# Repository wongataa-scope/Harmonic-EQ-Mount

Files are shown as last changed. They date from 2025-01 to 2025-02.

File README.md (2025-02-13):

This is my design for a GoTo telescope mount using strainwave gears (harmonic drives).  As strainwave gear telescope mounts, such as the ZWO AM5, started to become more available I thought why not make my own.

My mount is made from CNC machined aluminium, 3D printed aluminium, and 3D printed plastic.

The RA and DEC axes have a reduction ration of 450:1. The strainwave gears are 100:1 and there is 4:1 belt drive between the stepper motors and the strainwave gears.  The stepper motors are NEMA 17 size.

The strainwave gears are hollow so cables can pass through them.  This means there are no wires dangling off the telescope and mount.

The RA and DEC axes have hall sensors for automatic homing.

This mount has motorised altitude and azimuth axes so the mount does not have to be touched when polar aligning.  Everything is controlled by the computer controlling the mount.  The M4 ends of the azimuth and altitude leadscrews need to have thread locker applied before screwing into the parts they fit in to.  I use Loctite 243.

I have my mount connected to a EQ5 tripod.  The tripod interface will need to be modified if you wish to use a different tripod.  The 4040 aluminium extrusions do not have to be the length they are in the CAD files.  They can be any length.

I would recommend the CNC aluminium parts are made from 6061-T6 or 6082-T6 aluminium.  These grades are readily available, easily machined, and strong.  The T6 denotes the temper level.  T6 is stronger than non-tempered aluminium.
I used PETG for the 3D printed plastic.  I used heat set thread inserts in the 3D printed plastic where screws are screwed into them.

The first sheet of the BOM is a list of every part used.  The second sheet contains the BOMs broken down for each sub assembly.

The ‘Complete_Assembly_Neutral’ folder has a STEP and Parasolid file of the entire mount.

The ‘Solidworks_Makers_Files’ folder has the source Solidworks part, assembly, and drawing files.  These files were created in the Solidworks Makers version so cannot be opened with the educational or commercial versions of Solidworks.

The ‘Part_Drawing_PDF’ folder contains every drawing in PDF format.

The ‘3D_Print_Aluminium’ folder contains the files sent for aluminium 3D printing for the parts that underwent machining after printing.  These parts were machined on a lathe to fit bearings.

This is very much a version 1 design.  I’m sure there are ways it could be improved.  It hasn’t had much testing yet, but it does work.  I use the OpenAstroTech control system but it could also be made to work with OnStep.

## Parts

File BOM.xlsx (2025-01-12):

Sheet: Single BOM
1 | 2020 | 2020 ALUMINIUM EXTRUSION - 200 | 2 | https://ooznest.co.uk/product/20x20mm-t-v-slot-aluminium-extrusion-profile-silver-cut-to-size/
2 | 2040 | 2040 ALUMINIUM EXTRUSION - 150 | 2 | https://ooznest.co.uk/product/20x40mm-t-v-slot-aluminium-extrusion-profile-silver-cut-to-size/
3 | 4040 | 4040 ALUMINIUM EXTRUSION - 450 | 4 | https://ooznest.co.uk/product/40x40mm-t-v-slot-aluminium-extrusion-profile-silver-cut-to-size/
4 | 16 Pulley | PULLEY, GT2, 16 TOOTH | 2 | 16 Teeth, 5mm shaft, for 10mm belt |  |  | https://www.aliexpress.com/item/32995138803.html (https://www.igus.co.uk/iglidur-ibh/flanged-bearings/product-details/iglidur-g-m?artnr=GFM-0810-11)
5 | 17N13S1504FF5-200RS | AZ MOTOR | 2 | https://www.omc-stepperonline.com/nema-17-non-captive-acme-linear-stepper-motor-1-5a-34mm-stack-screw-lead-1-27mm-0-05-lead-length-200mm-17n13s1504ff5-200rs (https://www.igus.co.uk/iglidur-ibh/flanged-bearings/product-details/iglidur-g-m?artnr=GFM-0810-11)
6 | 30mm Shaft Support Seat | SUPPORT, SHAFT, 30MM | 1 | LFH 30 | https://www.aliexpress.com/item/4000088608614.html (https://www.igus.co.uk/iglidur-ibh/flanged-bearings/product-details/iglidur-g-m?artnr=GFM-0810-11)
7 | 5-M4-8 Shoulder screw |  | 1 | Berger Tools ISO7379-5-M4-8-NI |  |  | https://www.berger-tools.co.uk/Iso7379_Hexagon_Socket_Head_Shoulder_Screw_Ssb_Stainless/
8 | 72 Pulley Custom 3D Print | 72 PULLEY 3D PRINT | 2 | 3D Printed Plastic
9 | 72 Pulley Custom 3D Print Flange | 72 PULLEY FLANGE | 2 | 3D Printed Plastic
10 | Bearing Cover | BEARING COVER | 2 | 3D Printed Plastic
11 | Belt | BELT, GT2, 170 | 2 | 170 teeth 9mm wide |  | https://www.aliexpress.com/item/4000034021834.html
12 | Box Cable Guide 2 | BOX CABLE GUIDE | 1 | 3D Printed Plastic
13 | BUTTON HEAD M4x10 | SOCKET BUTTON HEAD, M4x10 | 32
14 | BUTTON HEAD M4x16 | SOCKET BUTTON HEAD M4x16 | 8
15 | BUTTON HEAD M4x20 | SOCKET BUTTON HEAD M4x20 | 2
16 | Cable Wedge | CABLE WEDGE | 1 | 3D Printed Plastic
17 | EQ5 Tripod Head | EQ5 TRIPOD HEAD | 1 | Part of tripod for reference
18 | Hall Effect Sensor | HALL EFFECT SENSOR | 2 | https://www.amazon.co.uk/WINGONEER-Effect-KY-003-Magnetic-Arduino/dp/B06XHG9CYN (https://www.igus.co.uk/iglidur-ibh/flanged-bearings/product-details/iglidur-g-m?artnr=GFM-0810-11)
19 | IGUS GFM-0810-11 | IGUS GFM-0810-11 | 4 | https://www.igus.co.uk/iglidur-ibh/flanged-bearings/product-details/iglidur-g-m?artnr=GFM-0810-11
20 | IGUS GFM-2023-11 | IGUS GFM-2023-11 | 2 | https://www.igus.co.uk/iglidur-ibh/flanged-bearings/product-details/iglidur-g-m?artnr=GFM-2023-11
21 | KFL08 | KFL08 BEARING | 2
22 | M10x55 | BOLT, HEX HD M10x55 | 1
23 | M3x10 | SCREW, SS SKT HD CAP M3x10 | 4
24 | M3x12 | SCREW, SS SKT HD CAP M3x12 | 4
25 | M3x20 | SCREW, SS SKT HD CAP M3x20 | 2
26 | M3x25 | SCREW, SS SKT HD CAP M3x25 | 34
27 | M3x30 | SCREW, SS SKT HD CAP M3x30 | 24
28 | M3x8 | SCREW, SS SKT HD CAP M3x8 | 12
29 | M4 Female Rod End Dia 5 Hole |  | 1 | Berger Tools GN648.1-5-M4-W |  |  | https://www.berger-tools.co.uk/Gn6481_Ball_Joint_Head_Female_Thread_Steel_Or_Steel_And_Brass/
30 | M4 WASHER | WASHER, SS STD HVY M4 | 4
31 | M4x10 | SCREW, SS SKT HD CAP M4x10 | 8
32 | M4x12 | SCREW, SS SKT HD CAP M4x12 | 20
33 | M5x10 | SCREW, SS SKT HD CAP M5x10 | 8
34 | M5x16 | M5x16 SS BUTTON HEAD | 36
35 | M5x25 | SCREW, SS SKT HD CAP M5x25 | 16
36 | M6x10 | SCREW, SS SKT HD CAP M6x10 | 8
37 | M6x20 | SCREW, SS SKT HD CAP M6x20 | 4
38 | M8 WASHER | WASHER, SS STD HVY M8 | 2
39 | M8x20 | SCREW, SS SKT HD CAP M8x20 | 2
40 | Magnet | MAGNET | 2 | https://www.amazon.co.uk/dp/B097MJLY51 (https://www.igus.co.uk/iglidur-ibh/flanged-bearings/product-details/iglidur-g-m?artnr=GFM-0810-11)
41 | Magnet Holder | MAGNET HOLDER | 2 | 3D Printed Plastic
42 | ML-EQHD-001 | DEC BEARING PLATE | 1 | 6061-T6 or 6082-T6 Aluminium
43 | ML-EQHD-002 | RA BEARING PLATE | 1 | 6061-T6 or 6082-T6 Aluminium
44 | ML-EQHD-003 | COUNTERWEIGHT PLATE | 1 | 6061-T6 or 6082-T6 Aluminium
45 | ML-EQHD-004 | TOP PLATE | 1 | 6061-T6 or 6082-T6 Aluminium
46 | ML-EQHD-005 | SIDE PLATE | 2 | 6061-T6 or 6082-T6 Aluminium
47 | ML-EQHD-006 | DEC PLATE | 1 | 6061-T6 or 6082-T6 Aluminium
48 | ML-EQHD-007 | VIXEN CLAMP PLATE | 1 | 6061-T6 or 6082-T6 Aluminium
49 | ML-EQHD-008 | RA PLATE | 1 | 6061-T6 or 6082-T6 Aluminium
50 | ML-EQHD-009 | RA SIDE PLATE | 2 | 6061-T6 or 6082-T6 Aluminium
51 | ML-EQHD-010 | ALT PIVOT UPRIGHT | 2 | 6061-T6 or 6082-T6 Aluminium
52 | ML-EQHD-011 | ALT PIVOT BASE | 1 | 6061-T6 or 6082-T6 Aluminium
53 | ML-EQHD-013 | AZ FRAME BASE | 1 | 6061-T6 or 6082-T6 Aluminium
54 | ML-EQHD-014 | UPPER TRIPOD CONNECTION PLATE | 1 | 6061-T6 or 6082-T6 Aluminium
55 | ML-EQHD-015 | LOWER TRIPOD CONNECTION PLATE | 1 | 6061-T6 or 6082-T6 Aluminium
56 | ML-EQHD-016 | UPPER AZ MOTOR MOUNT | 1 | 6061-T6 or 6082-T6 Aluminium
57 | ML-EQHD-017 | LOWER AZ MOTOR MOUNT | 1
58 | ML-EQHD-018 | ALT PIVOT SHAFT | 1 | 6061-T6 or 6082-T6 Aluminium
59 | ML-EQHD-019 | LEADSCREW END PIVOT | 1 | 3D Printed aluminium, then machined
60 | ML-EQHD-020 | AZ MOTOR MOUNT | 1 | 3D Printed aluminium, then machined
61 | ML-EQHD-021 | AZ PIN BLOCK | 1
62 | ML-EQHD-022 | AZ MOTOR MOUNT | 1 | 3D Printed aluminium, then machined
63 | Motor Bracket MC Box | MOUNT, MOTOR, NEMA 17 | 2
64 | NEMA 17 Stepper | MOTOR, STEPPER, NEMA 17 | 2
65 | SHG-17-100-2UH | GEAR, STRAINWAVE | 2 | HBK17 100:1 |  | https://www.aliexpress.com/item/1005006392747447.html (https://www.igus.co.uk/iglidur-ibh/flanged-bearings/product-details/iglidur-g-m?artnr=GFM-0810-11)
66 | SKF_51100 | 51100 THRUST BEARING | 1
67 | SKF_51115 | 51115 THRUST BEARING | 1
68 | Tee-Nut | T NUT M5 | 28
69 | Tee-Nut | T NUT M4 | 8
70 | Thrust Bearing Cover | THRUST BEARING COVER | 1 | 3D Printed Plastic
71 | Vixen Clamp | VIXEN DOVETAIL CLAMP | 2 | https://www.firstlightoptics.com/dovetails-saddles-clamps/astro-essentials-mini-vixen-style-dovetail-clamp.html (https://www.igus.co.uk/iglidur-ibh/flanged-bearings/product-details/iglidur-g-m?artnr=GFM-0810-11)

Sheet: Assembly BOMs
Mount Complete
ITEM NO. | PART NUMBER | DESCRIPTION | QTY.
1 | Axis Box MC Parts | AXIS BOX | 1 | Assembly
2 | DEC Assy | DEC ASSEMBLY | 1 | Assembly
3 | M3x25 | SCREW, SS SKT HD CAP M3x25 | 32
4 | RA Tilt Assy | RA TILT ASSEMBLY | 1 | Assembly
5 | M5x16 | M5x16 SS BUTTON HEAD | 8
6 | Tee-Nut | T NUT M5 | 12
7 | Bearing Cover | BEARING COVER | 2 | 3D Printed Plastic
8 | BUTTON HEAD M4x10 | SOCKET BUTTON HEAD, M4x10 | 8
9 | Tripod Connection | TRIPOD CONNECTION | 1 | Assembly
10 | KFL08 | KFL08 BEARING | 2
11 | SKF_51100 | 51100 THRUST BEARING | 1
12 | M10x55 | BOLT, HEX HD M10x55 | 1
13 | AZ Frame Harmonic | AZ FRAME HARMONIC | 1 | Assembly
14 | ML-EQHD-021 | AZ PIN BLOCK | 1
15 | Hall Effect Sensor | HALL EFFECT SENSOR | 2 | https://www.amazon.co.uk/WINGONEER-Effect-KY-003-Magnetic-Arduino/dp/B06XHG9CYN (https://www.igus.co.uk/iglidur-ibh/flanged-bearings/product-details/iglidur-g-m?artnr=GFM-0810-11)
16 | 17N13S1504FF5-200RS | AZ MOTOR | 1 | https://www.omc-stepperonline.com/nema-17-non-captive-acme-linear-stepper-motor-1-5a-34mm-stack-screw-lead-1-27mm-0-05-lead-length-200mm-17n13s1504ff5-200rs (https://www.igus.co.uk/iglidur-ibh/flanged-bearings/product-details/iglidur-g-m?artnr=GFM-0810-11)
17 | ML-EQHD-022 | AZ MOTOR MOUNT | 1 | 3D Printed aluminium, then machined
18 | M3x10 | SCREW, SS SKT HD CAP M3x10 | 4
19 | M4 Female Rod End Dia 5 Hole |  | 1 | Berger Tools GN648.1-5-M4-W |  |  | https://www.berger-tools.co.uk/Gn6481_Ball_Joint_Head_Female_Thread_Steel_Or_Steel_And_Brass/
20 | 5-M4-8 Shoulder screw |  | 1 | Berger Tools ISO7379-5-M4-8-NI |  |  | https://www.berger-tools.co.uk/Iso7379_Hexagon_Socket_Head_Shoulder_Screw_Ssb_Stainless/
21 | Thrust Bearing Cover | THRUST BEARING COVER | 1 | 3D Printed Plastic
22 | M4 WASHER | WASHER, SS STD HVY M4 | 4
23 | M4x12 | SCREW, SS SKT HD CAP M4x12 | 4
24 | BUTTON HEAD M4x20 | SOCKET BUTTON HEAD M4x20 | 2
25 | M5x16 | SCREW, SS SKT HD CAP M5x16 | 4
Axis Box MC Parts
ITEM NO. | Number | DESCRIPTION | QTY.
1 | ML-EQHD-001 | DEC BEARING PLATE | 1 | 6061-T6 or 6082-T6 Aluminium
2 | ML-EQHD-002 | RA BEARING PLATE | 1 | 6061-T6 or 6082-T6 Aluminium
3 | SHG-17-100-2UH | GEAR, STRAINWAVE | 2 | HBK17 100:1 |  | https://www.aliexpress.com/item/1005006392747447.html (https://www.igus.co.uk/iglidur-ibh/flanged-bearings/product-details/iglidur-g-m?artnr=GFM-0810-11)
4 | 72 Pulley Custom 3D Print | 72 PULLEY 3D PRINT | 2 | 3D Printed Plastic
5 | 72 Pulley Custom 3D Print Flange | 72 PULLEY FLANGE | 2 | 3D Printed Plastic
6 | M3x8 | SCREW, SS SKT HD CAP M3x8 | 6
7 | ML-EQHD-003 | COUNTERWEIGHT PLATE | 1 | 6061-T6 or 6082-T6 Aluminium
8 | 16 Pulley | PULLEY, GT2, 16 TOOTH | 2 | 16 Teeth, 5mm shaft, for 10mm belt |  |  | https://www.aliexpress.com/item/32995138803.html (https://www.igus.co.uk/iglidur-ibh/flanged-bearings/product-details/iglidur-g-m?artnr=GFM-0810-11)
9 | Belt | BELT, GT2, 170 | 2 | 170 teeth 9mm wide |  | https://www.aliexpress.com/item/4000034021834.html
10 | NEMA 17 Stepper | MOTOR, STEPPER, NEMA 17 | 2
11 | ML-EQHD-004 | TOP PLATE | 1 | 6061-T6 or 6082-T6 Aluminium
12 | Motor Bracket MC Box | MOUNT, MOTOR, NEMA 17 | 2
13 | ML-EQHD-005 | SIDE PLATE | 2 | 6061-T6 or 6082-T6 Aluminium
14 | 30mm Shaft Support Seat | SUPPORT, SHAFT, 30MM | 1 | LFH 30 | https://www.aliexpress.com/item/4000088608614.html (https://www.igus.co.uk/iglidur-ibh/flanged-bearings/product-details/iglidur-g-m?artnr=GFM-0810-11)
15 | M6x20 | SCREW, SS SKT HD CAP M6x20 | 4
16 | M3x30 | SCREW, SS SKT HD CAP M3x30 | 24
17 | M4x12 | SCREW, SS SKT HD CAP M4x12 | 8
18 | BUTTON HEAD M4x10 | SOCKET BUTTON HEAD, M4x10 | 24
19 | M3x25 | SCREW, SS SKT HD CAP M3x25 | 2
20 | Box Cable Guide 2 | BOX CABLE GUIDE | 1 | 3D Printed Plastic
21 | M3x20 | SCREW, SS SKT HD CAP M3x20 | 2
DEC Assy
ITEM NO. | PART NUMBER | DESCRIPTION | QTY.
1 | ML-EQHD-006 | DEC PLATE | 1 | 6061-T6 or 6082-T6 Aluminium
2 | 2020 | 2020 ALUMINIUM EXTRUSION - 200 | 2 | https://ooznest.co.uk/product/20x20mm-t-v-slot-aluminium-extrusion-profile-silver-cut-to-size/
3 | Tee-Nut | T NUT M5 | 8
4 | M5x16 | M5x16 SS BUTTON HEAD | 8
5 | ML-EQHD-007 | VIXEN CLAMP PLATE | 1 | 6061-T6 or 6082-T6 Aluminium
6 | Vixen Clamp | VIXEN DOVETAIL CLAMP | 2 | https://www.firstlightoptics.com/dovetails-saddles-clamps/astro-essentials-mini-vixen-style-dovetail-clamp.html (https://www.igus.co.uk/iglidur-ibh/flanged-bearings/product-details/iglidur-g-m?artnr=GFM-0810-11)
7 | M6x10 | SCREW, SS SKT HD CAP M6x10 | 8
8 | M4x10 | SCREW, SS SKT HD CAP M4x10 | 8
9 | Tee-Nut | T NUT M4 | 8
10 | Magnet Holder | MAGNET HOLDER | 1 | 3D Printed Plastic
11 | Magnet | MAGNET | 1 | https://www.amazon.co.uk/dp/B097MJLY51 (https://www.igus.co.uk/iglidur-ibh/flanged-bearings/product-details/iglidur-g-m?artnr=GFM-0810-11)
12 | M3x8 | SCREW, SS SKT HD CAP M3x8 | 2
RA Tilt Assy
ITEM NO. | PART NUMBER | DESCRIPTION | QTY.
1 | ML-EQHD-008 | RA PLATE | 1 | 6061-T6 or 6082-T6 Aluminium
2 | ML-EQHD-009 | RA SIDE PLATE | 2 | 6061-T6 or 6082-T6 Aluminium
3 | BUTTON HEAD M4x16 | SOCKET BUTTON HEAD M4x16 | 8
4 | IGUS GFM-2023-11 | IGUS GFM-2023-11 | 2 | https://www.igus.co.uk/iglidur-ibh/flanged-bearings/product-details/iglidur-g-m?artnr=GFM-2023-11
5 | ML-EQHD-010 | ALT PIVOT UPRIGHT | 2 | 6061-T6 or 6082-T6 Aluminium
6 | ML-EQHD-018 | ALT PIVOT SHAFT | 1 | 6061-T6 or 6082-T6 Aluminium
7 | M8 WASHER | WASHER, SS STD HVY M8 | 2
8 | M8x20 | SCREW, SS SKT HD CAP M8x20 | 2
9 | ML-EQHD-011 | ALT PIVOT BASE | 1 | 6061-T6 or 6082-T6 Aluminium
10 | M4x12 | SCREW, SS SKT HD CAP M4x12 | 8
11 | ML-EQHD-019 | LEADSCREW END PIVOT | 1 | 3D Printed aluminium, then machined
12 | 17N13S1504FF5-200RS | AZ MOTOR | 1 | https://www.omc-stepperonline.com/nema-17-non-captive-acme-linear-stepper-motor-1-5a-34mm-stack-screw-lead-1-27mm-0-05-lead-length-200mm-17n13s1504ff5-200rs (https://www.igus.co.uk/iglidur-ibh/flanged-bearings/product-details/iglidur-g-m?artnr=GFM-0810-11)
13 | ML-EQHD-020 | AZ MOTOR MOUNT | 1 | 3D Printed aluminium, then machined
14 | IGUS GFM-0810-11 | IGUS GFM-0810-11 | 4 | https://www.igus.co.uk/iglidur-ibh/flanged-bearings/product-details/iglidur-g-m?artnr=GFM-0810-11
15 | Magnet Holder | MAGNET HOLDER | 1 | 3D Printed Plastic
16 | Magnet | MAGNET | 1 | https://www.amazon.co.uk/dp/B097MJLY51 (https://www.igus.co.uk/iglidur-ibh/flanged-bearings/product-details/iglidur-g-m?artnr=GFM-0810-11)
17 | M3x8 | SCREW, SS SKT HD CAP M3x8 | 2
18 | M3x12 | SCREW, SS SKT HD CAP M3x12 | 4
Tripod Connection
ITEM NO. | PART NUMBER | DESCRIPTION | QTY.
1 | EQ5 Tripod Head | EQ5 TRIPOD HEAD | 1 | Part of tripod for reference
2 | ML-EQHD-015 | LOWER TRIPOD CONNECTION PLATE | 1 | 6061-T6 or 6082-T6 Aluminium
3 | 4040 | 4040 ALUMINIUM EXTRUSION - 450 | 4 | https://ooznest.co.uk/product/40x40mm-t-v-slot-aluminium-extrusion-profile-silver-cut-to-size/
4 | M5x16 | SCREW, SS SKT HD CAP M5x16 | 16
5 | ML-EQHD-014 | UPPER TRIPOD CONNECTION PLATE | 1 | 6061-T6 or 6082-T6 Aluminium
6 | ML-EQHD-016 | UPPER AZ MOTOR MOUNT | 1 | 6061-T6 or 6082-T6 Aluminium
7 | M5x25 | SCREW, SS SKT HD CAP M5x25 | 16
8 | SKF_51115 | 51115 THRUST BEARING | 1
9 | ML-EQHD-017 | LOWER AZ MOTOR MOUNT | 1
AZ Frame Harmonic
ITEM NO. | PART NUMBER | DESCRIPTION | QTY.
1 | ML-EQHD-013 | AZ FRAME BASE | 1 | 6061-T6 or 6082-T6 Aluminium
2 | 2040 | 2040 ALUMINIUM EXTRUSION - 150 | 2 | https://ooznest.co.uk/product/20x40mm-t-v-slot-aluminium-extrusion-profile-silver-cut-to-size/
3 | Tee-Nut | T NUT M5 | 8
4 | M5x10 | SCREW, SS SKT HD CAP M5x10 | 8
5 | Cable Wedge | CABLE WEDGE | 1 | 3D Printed Plastic
6 | M3x8 | SCREW, SS SKT HD CAP M3x8 | 2

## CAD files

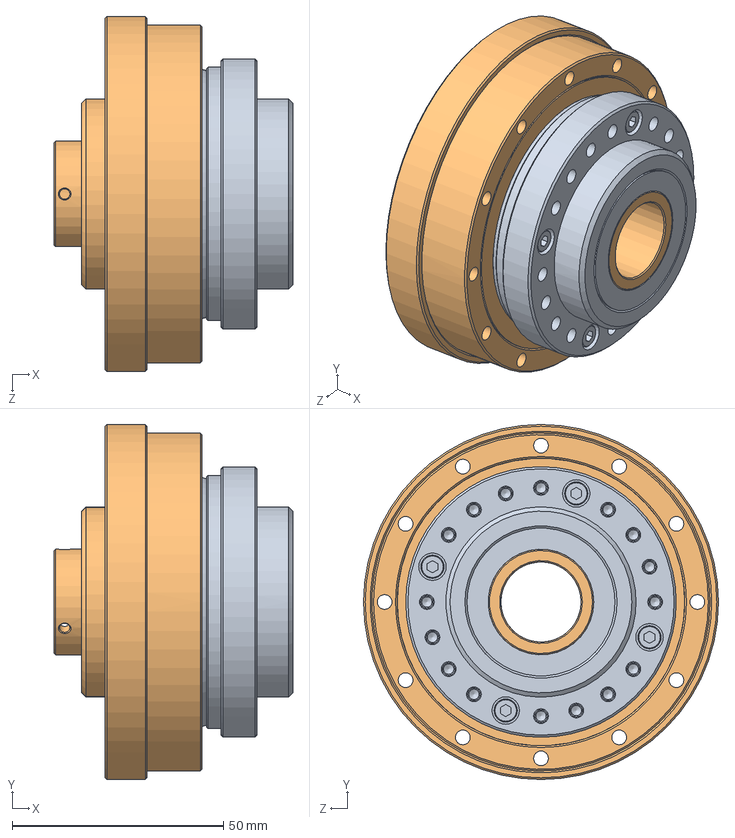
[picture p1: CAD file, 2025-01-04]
Solidworks_Makers_Files/SHG-17-100-2UH.SLDASM
56.5 x 84.0 x 84.0 mm
SHF_SHG-17-xxx-2UH-Part1
SHF_SHG-17-xxx-2UH-Part2

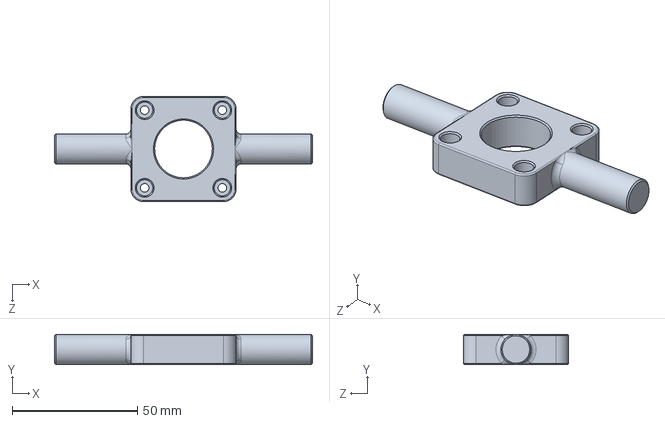
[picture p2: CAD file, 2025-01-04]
3D_Print_Aluminium/ML-EQHD-022 3D Print Al.STEP
103.0 x 12.0 x 42.0 mm

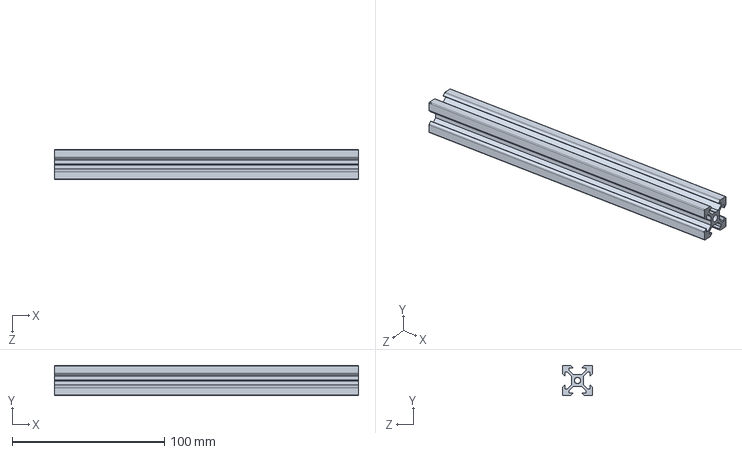
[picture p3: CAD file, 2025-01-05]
Solidworks_Makers_Files/2020.SLDPRT
200.0 x 20.0 x 20.0 mm

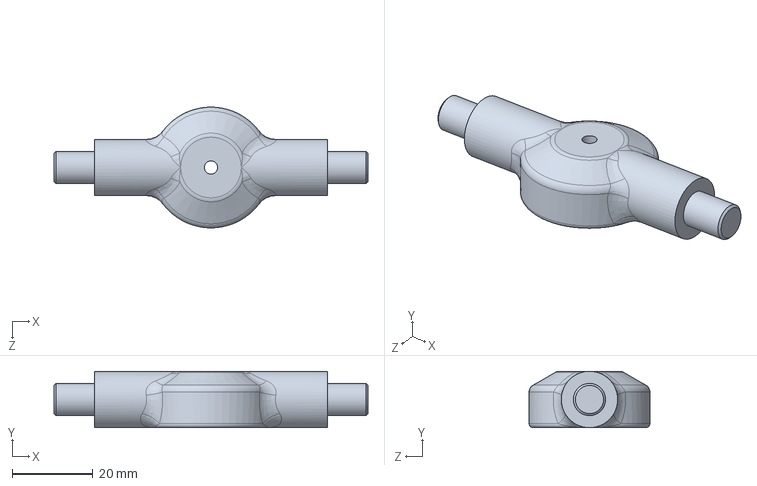
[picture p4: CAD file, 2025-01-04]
3D_Print_Aluminium/ML-EQHD-019 3D Print Al.STEP
78.0 x 14.0 x 30.0 mm

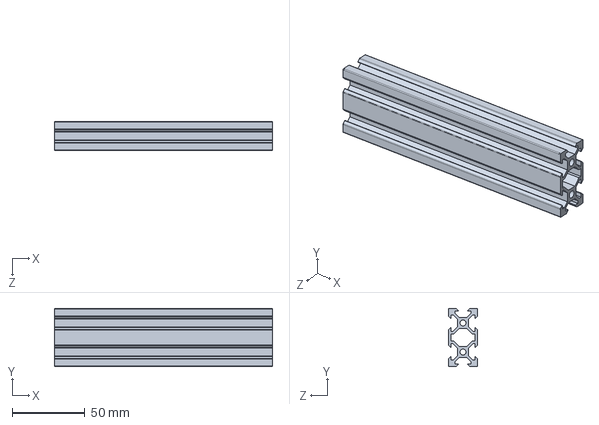
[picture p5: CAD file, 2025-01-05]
Solidworks_Makers_Files/2040.SLDPRT
150.0 x 40.0 x 20.0 mm

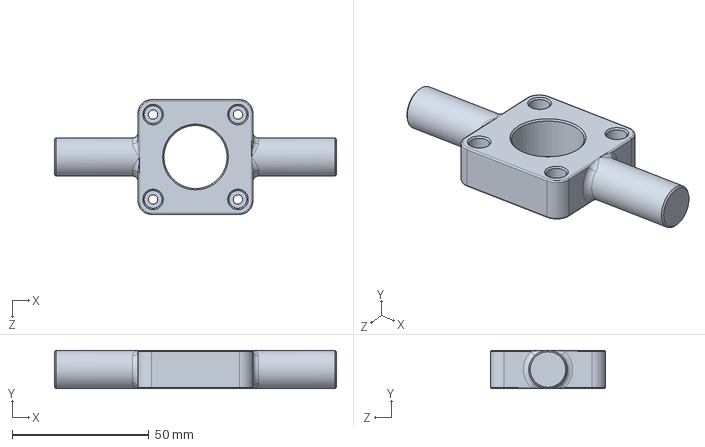
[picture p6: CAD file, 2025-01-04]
3D_Print_Aluminium/ML-EQHD-020 3D Print Al.STEP
103.0 x 14.0 x 42.0 mm

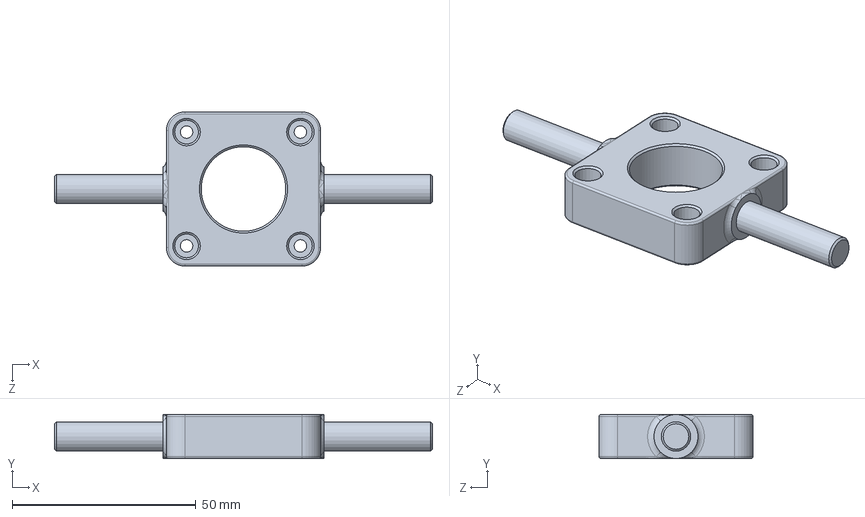
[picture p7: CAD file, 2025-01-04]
Solidworks_Makers_Files/ML-EQHD-022.SLDPRT
103.0 x 12.0 x 42.0 mm

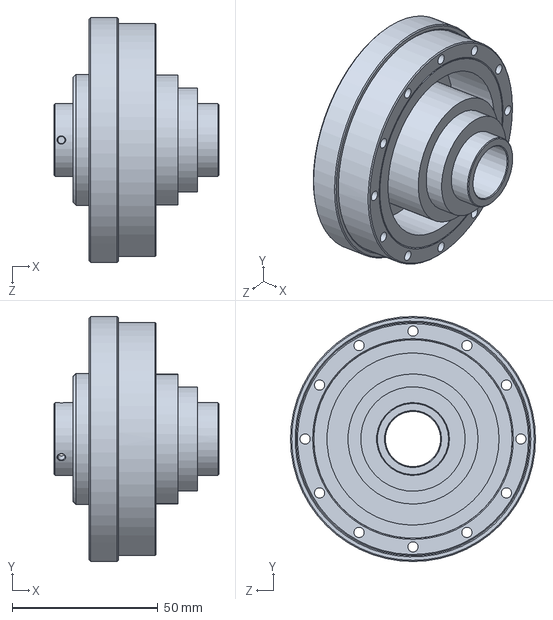
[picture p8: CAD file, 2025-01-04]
Solidworks_Makers_Files/SHF_SHG-17-xxx-2UH-Part1.SLDPRT
56.5 x 84.0 x 84.0 mm

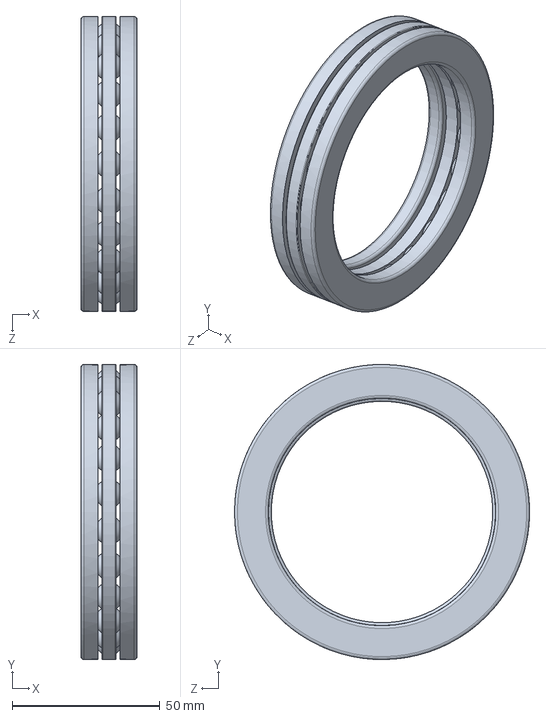
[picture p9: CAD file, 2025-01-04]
Solidworks_Makers_Files/SKF_51115.SLDPRT
19.0 x 100.0 x 100.0 mm

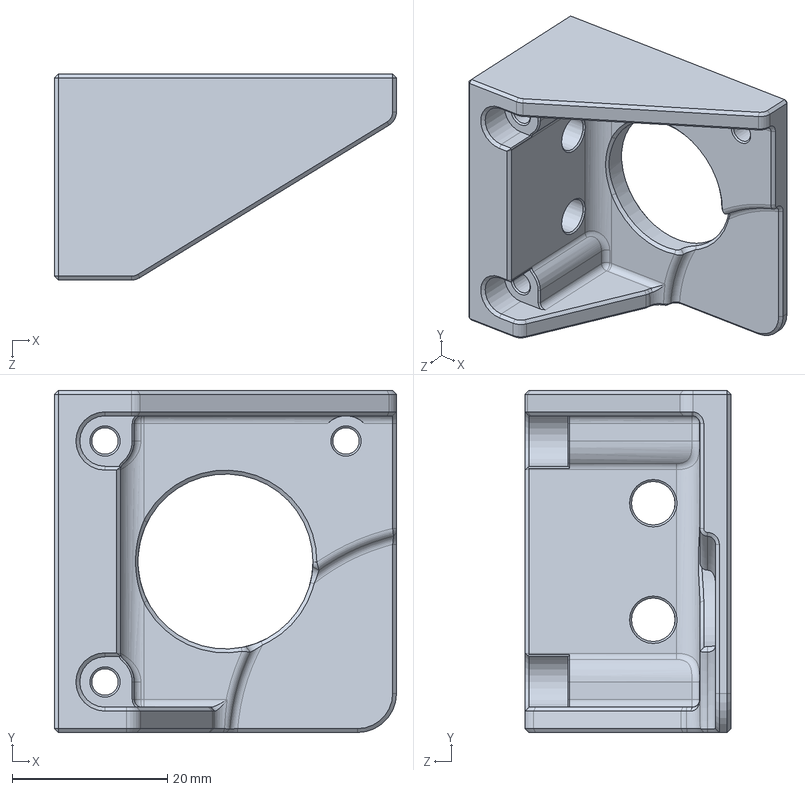
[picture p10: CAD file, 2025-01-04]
Solidworks_Makers_Files/Motor Bracket MC Box.SLDPRT
44.0 x 44.0 x 26.5 mm

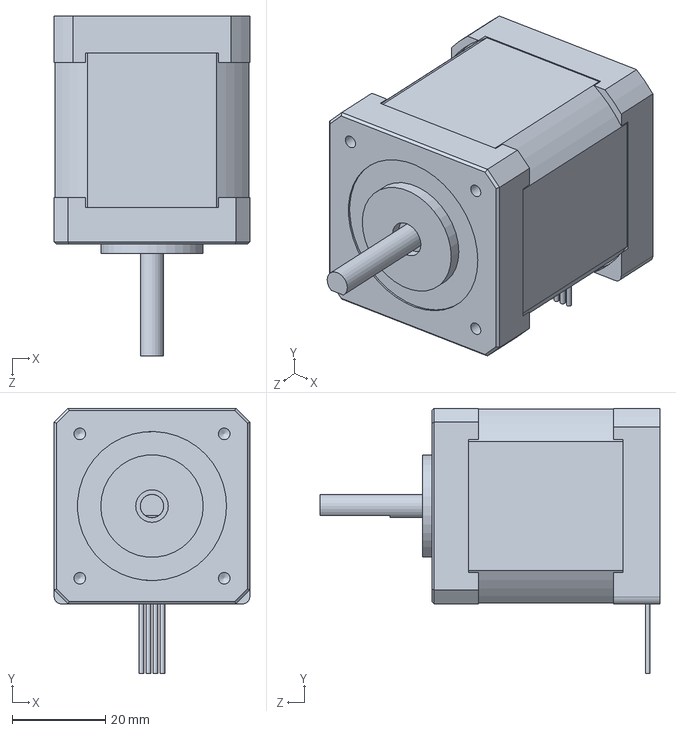
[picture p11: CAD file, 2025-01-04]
Solidworks_Makers_Files/NEMA 17 Stepper.SLDPRT
42.0 x 57.0 x 73.0 mm

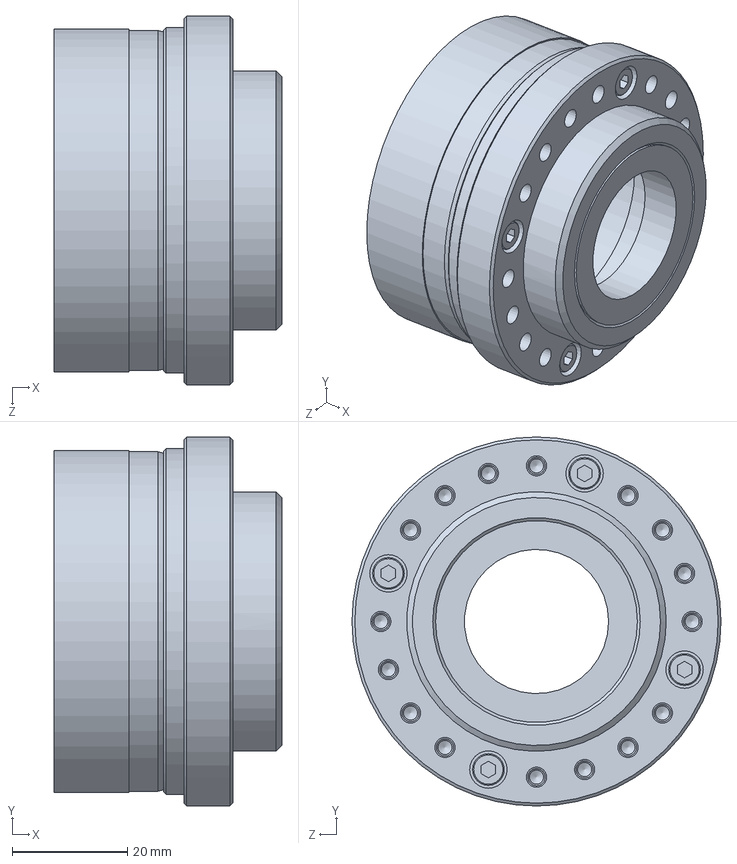
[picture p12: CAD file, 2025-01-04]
Solidworks_Makers_Files/SHF_SHG-17-xxx-2UH-Part2.SLDPRT
39.5 x 64.0 x 64.0 mm

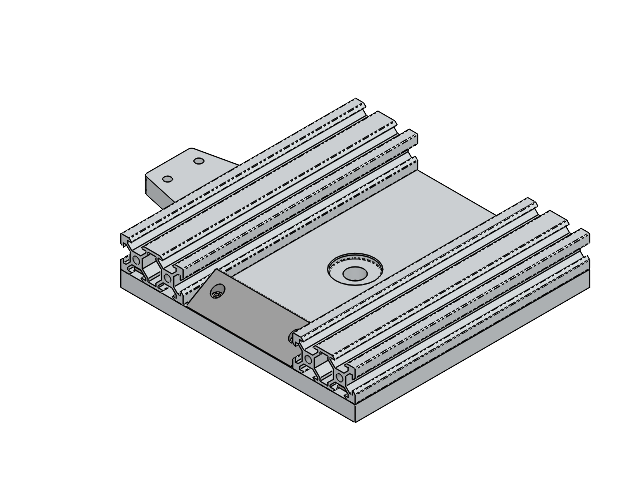
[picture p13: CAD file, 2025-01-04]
Solidworks_Makers_Files/AZ Frame Harmonic.SLDASM
ML-EQHD-013
Tee-Nut x 8
M5 SS SHCS x 8
Cable Wedge
M3 SS SHCS x 2

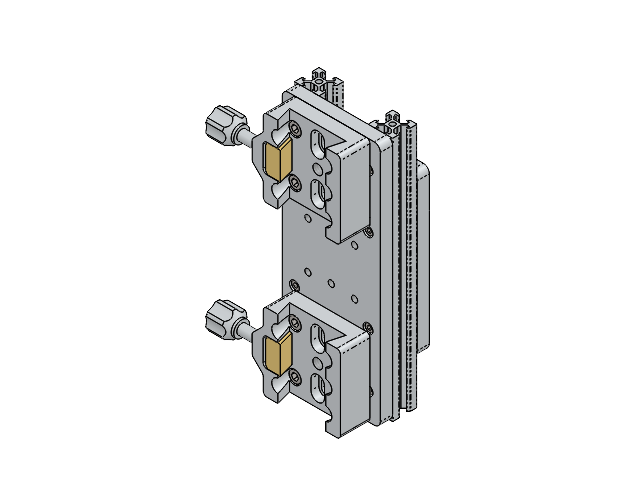
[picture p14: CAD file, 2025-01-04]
Solidworks_Makers_Files/DEC Assy.SLDASM
ML-EQHD-006
Tee-Nut x 16
M5 SS Button Head x 8
ML-EQHD-007
Vixen Clamp x 2
M6 SS SHCS x 8
M4 SS SHCS x 8
Magnet Holder
Magnet
M3 SS SHCS x 2

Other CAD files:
Complete_Assembly_Neutral/Mount Complete.STEP
Solidworks_Makers_Files/Tripod Connection.SLDASM
Solidworks_Makers_Files/RA Tilt Assy.SLDASM
Solidworks_Makers_Files/Axis Box MC Parts.SLDASM
Solidworks_Makers_Files/16 Pulley.SLDPRT
Solidworks_Makers_Files/17N13S1504FF5-200RS Shaft.SLDPRT
Solidworks_Makers_Files/17N13S1504FF5-200RS.SLDPRT
Solidworks_Makers_Files/30mm Shaft Support Seat.SLDPRT
Solidworks_Makers_Files/4040.SLDPRT
Solidworks_Makers_Files/5-M4-8 Shoulder screw.SLDPRT
Solidworks_Makers_Files/72 Pulley Custom 3D Print Flange.SLDPRT
Solidworks_Makers_Files/72 Pulley Custom 3D Print.SLDPRT
Solidworks_Makers_Files/AZ Frame Harmonic.SLDDRW
Solidworks_Makers_Files/Axis Box MC Parts.SLDDRW
Solidworks_Makers_Files/Bearing Cover.SLDPRT
Solidworks_Makers_Files/Belt.SLDPRT
Solidworks_Makers_Files/Box Cable Guide 2.SLDPRT
Solidworks_Makers_Files/Cable Wedge.SLDPRT
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

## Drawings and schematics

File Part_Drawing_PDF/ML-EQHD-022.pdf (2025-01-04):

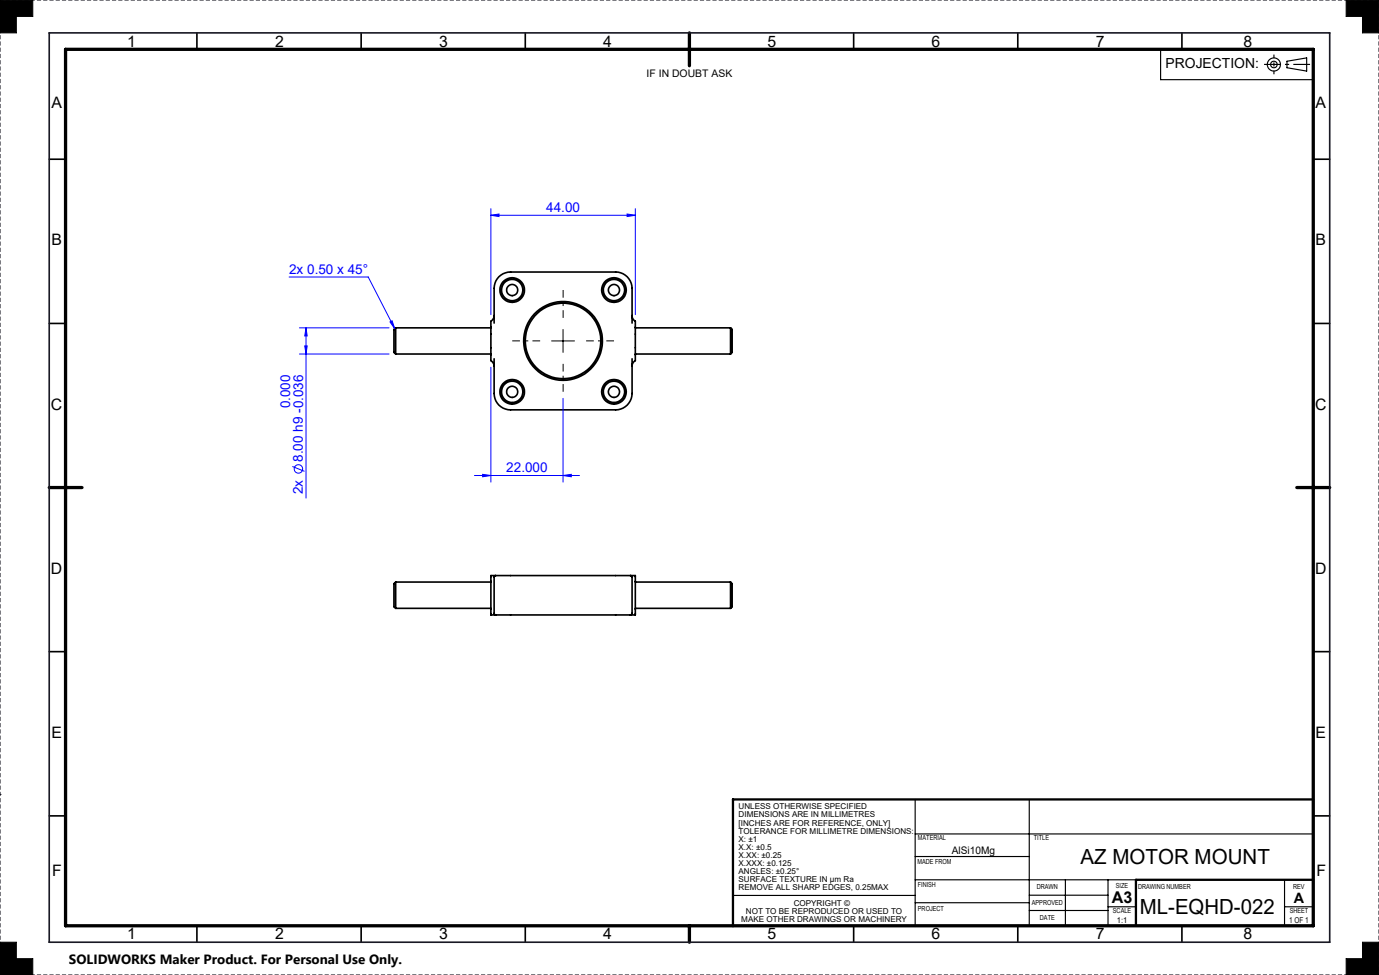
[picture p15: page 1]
DRAWING NUMBER; A3 DRAWN; MADE FROM

IF IN DOUBT ASK

UNLESS OTHERWISE SPECIFIED DIMENSIONS ARE IN MILLIMETRES [INCHES ARE FOR REFERENCE, ONLY] TOLERANCE FOR MILLIMETRE DIMENSIONS: X: ±1 X.X: ±0.5 X.XX: ±0.25 X.XXX: ±0.125 ANGLES: ±0.25° SURFACE TEXTURE IN μm Ra REMOVE ALL SHARP EDGES, 0.25MAX

AZ MOTOR MOUNT

COPYRIGHT © NOT TO BE REPRODUCED OR USED TO MAKE OTHER DRAWINGS OR MACHINERY | APPROVED

DATE

1:1 | SHEET

SOLIDWORKS Maker Product. For Personal Use Only.

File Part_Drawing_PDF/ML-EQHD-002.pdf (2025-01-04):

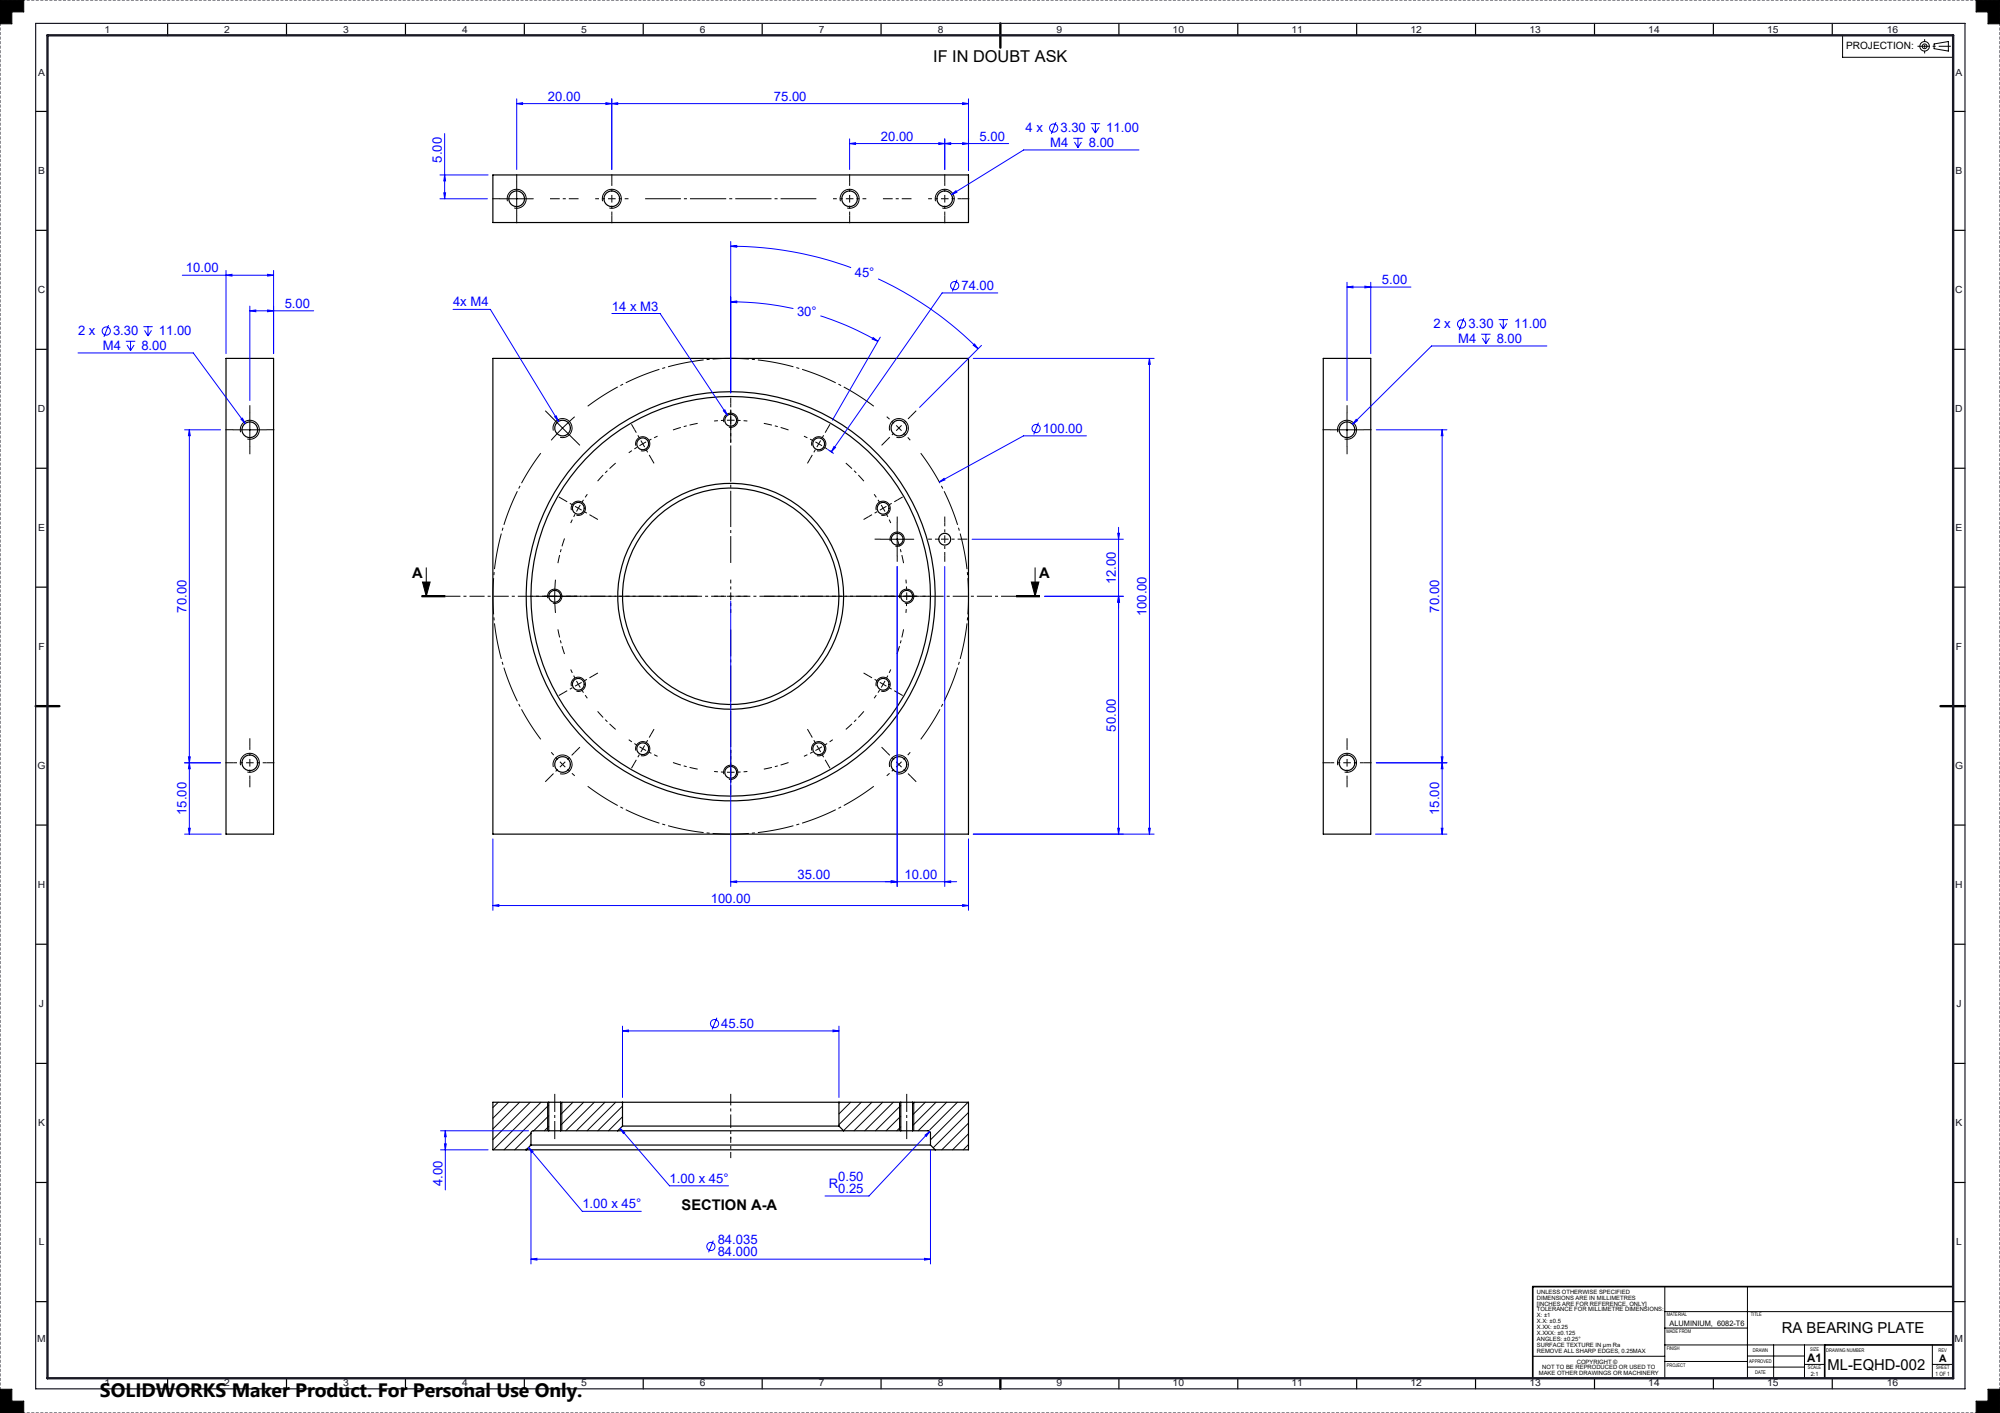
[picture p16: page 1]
1.00 x 45° SECTION A-A; DRAWING NUMBER; A1 DRAWN; MADE FROM; ALUMINIUM, 6082-T6; COPYRIGHT ©; MAKE OTHER DRAWINGS OR MACHINERY

IF IN DOUBT ASK

UNLESS OTHERWISE SPECIFIED
DIMENSIONS ARE IN MILLIMETRES
[INCHES ARE FOR REFERENCE, ONLY]
TOLERANCE FOR MILLIMETRE DIMENSIONS:
X.XXX: ±0.125
ANGLES: ±0.25°
SURFACE TEXTURE IN μm Ra
REMOVE ALL SHARP EDGES, 0.25MAX

RA BEARING PLATE

SOLIDWORKS Maker Product. For Personal Use Only.

NOT TO BE REPRODUCED OR USED TO

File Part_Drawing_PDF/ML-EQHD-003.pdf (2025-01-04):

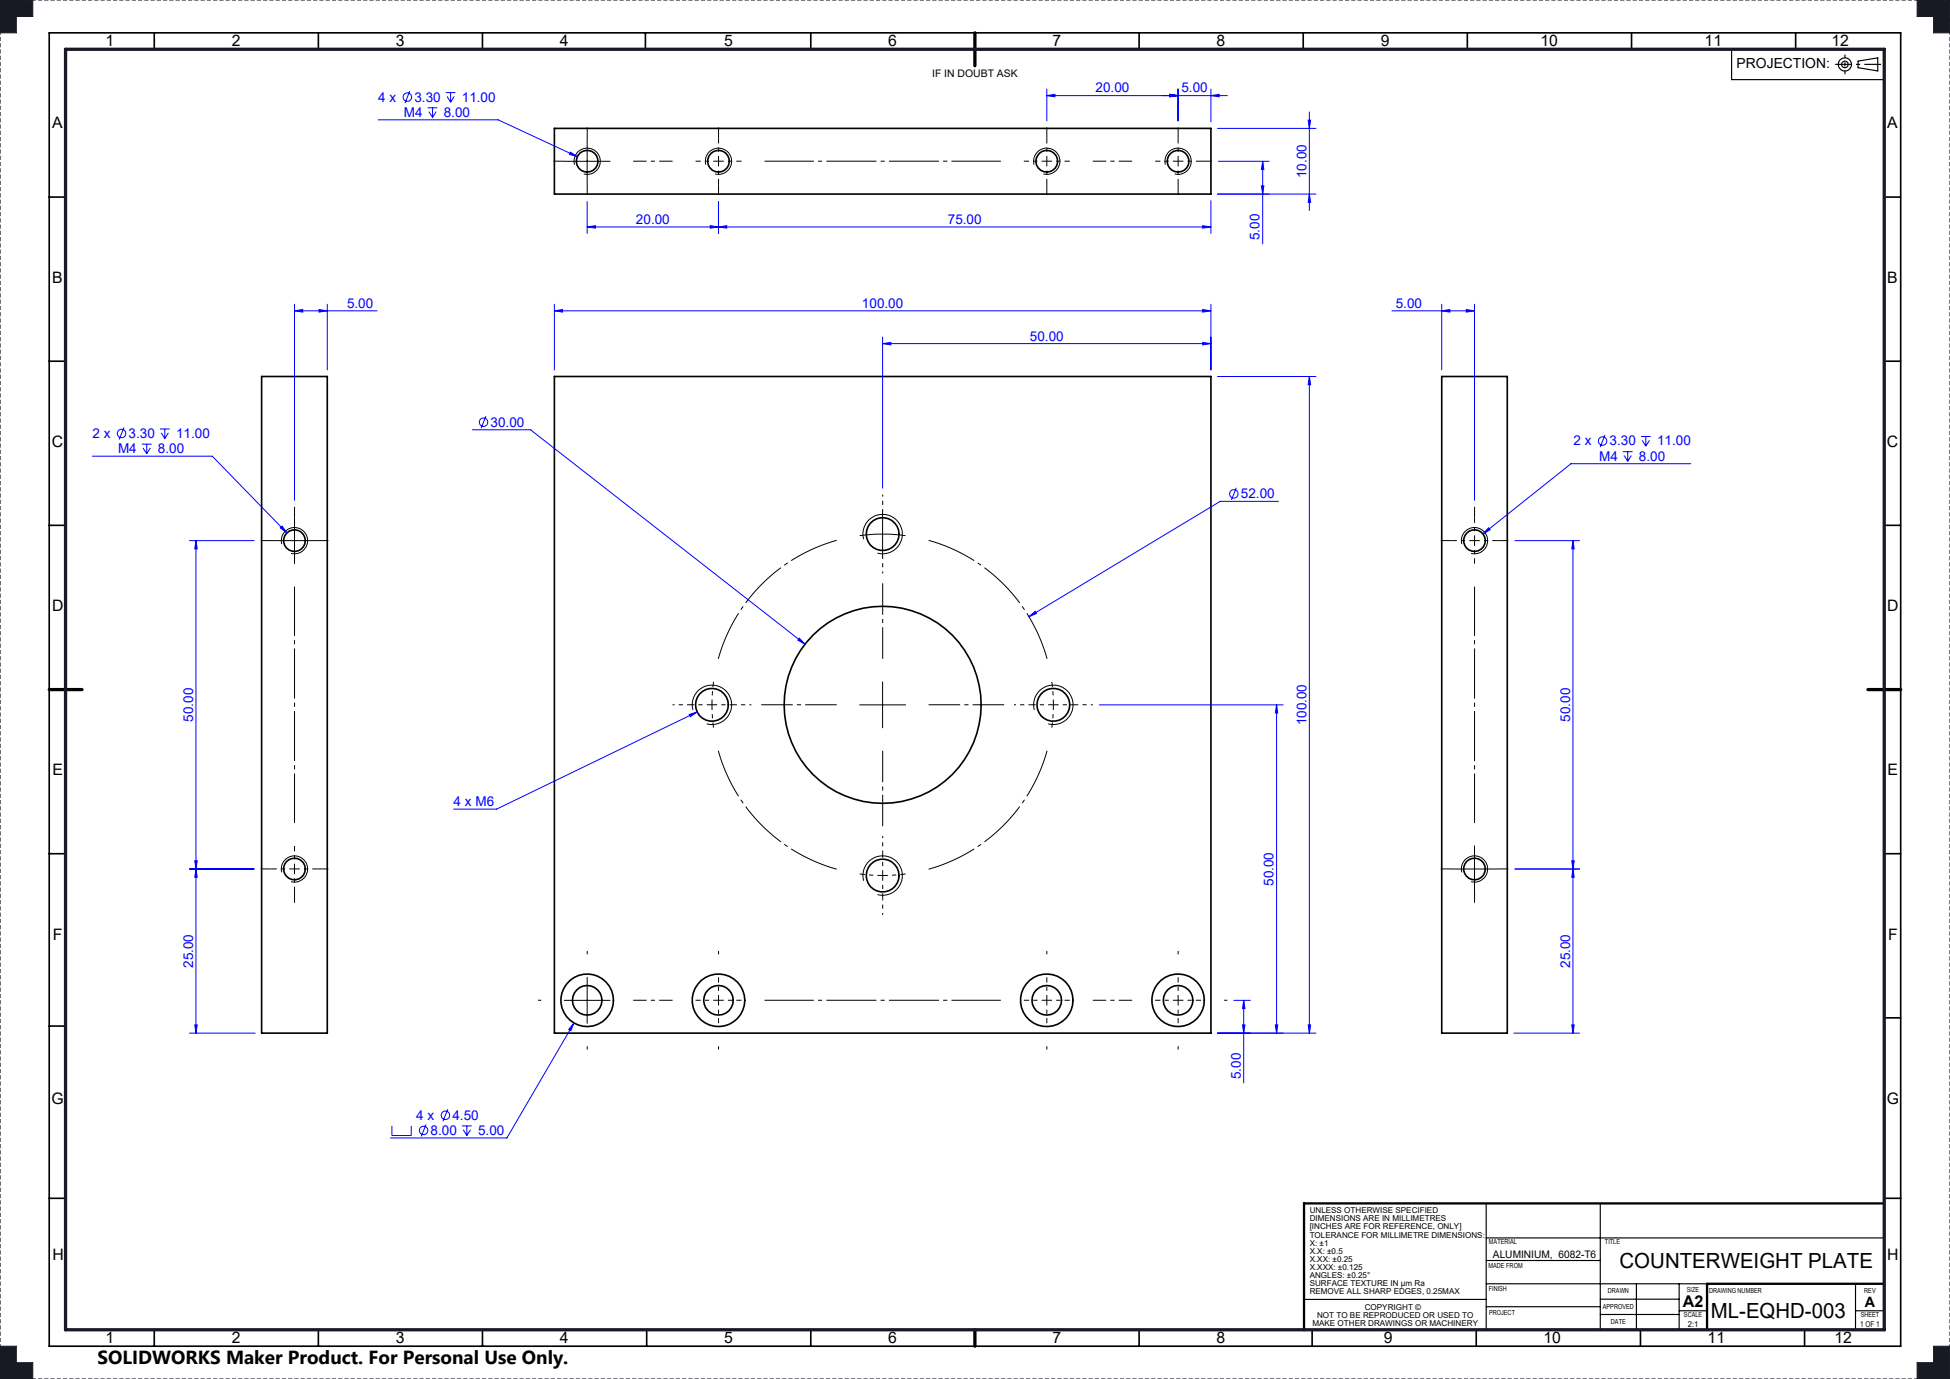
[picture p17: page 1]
COPYRIGHT ©; ALUMINIUM, 6082-T6 MADE FROM; DRAWING NUMBER; SCALE; ML-EQHD-003 A; COUNTERWEIGHT PLATE

IF IN DOUBT ASK

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

NOT TO BE REPRODUCED OR USED TO
MAKE OTHER DRAWINGS OR MACHINERY

SOLIDWORKS Maker Product. For Personal Use Only.

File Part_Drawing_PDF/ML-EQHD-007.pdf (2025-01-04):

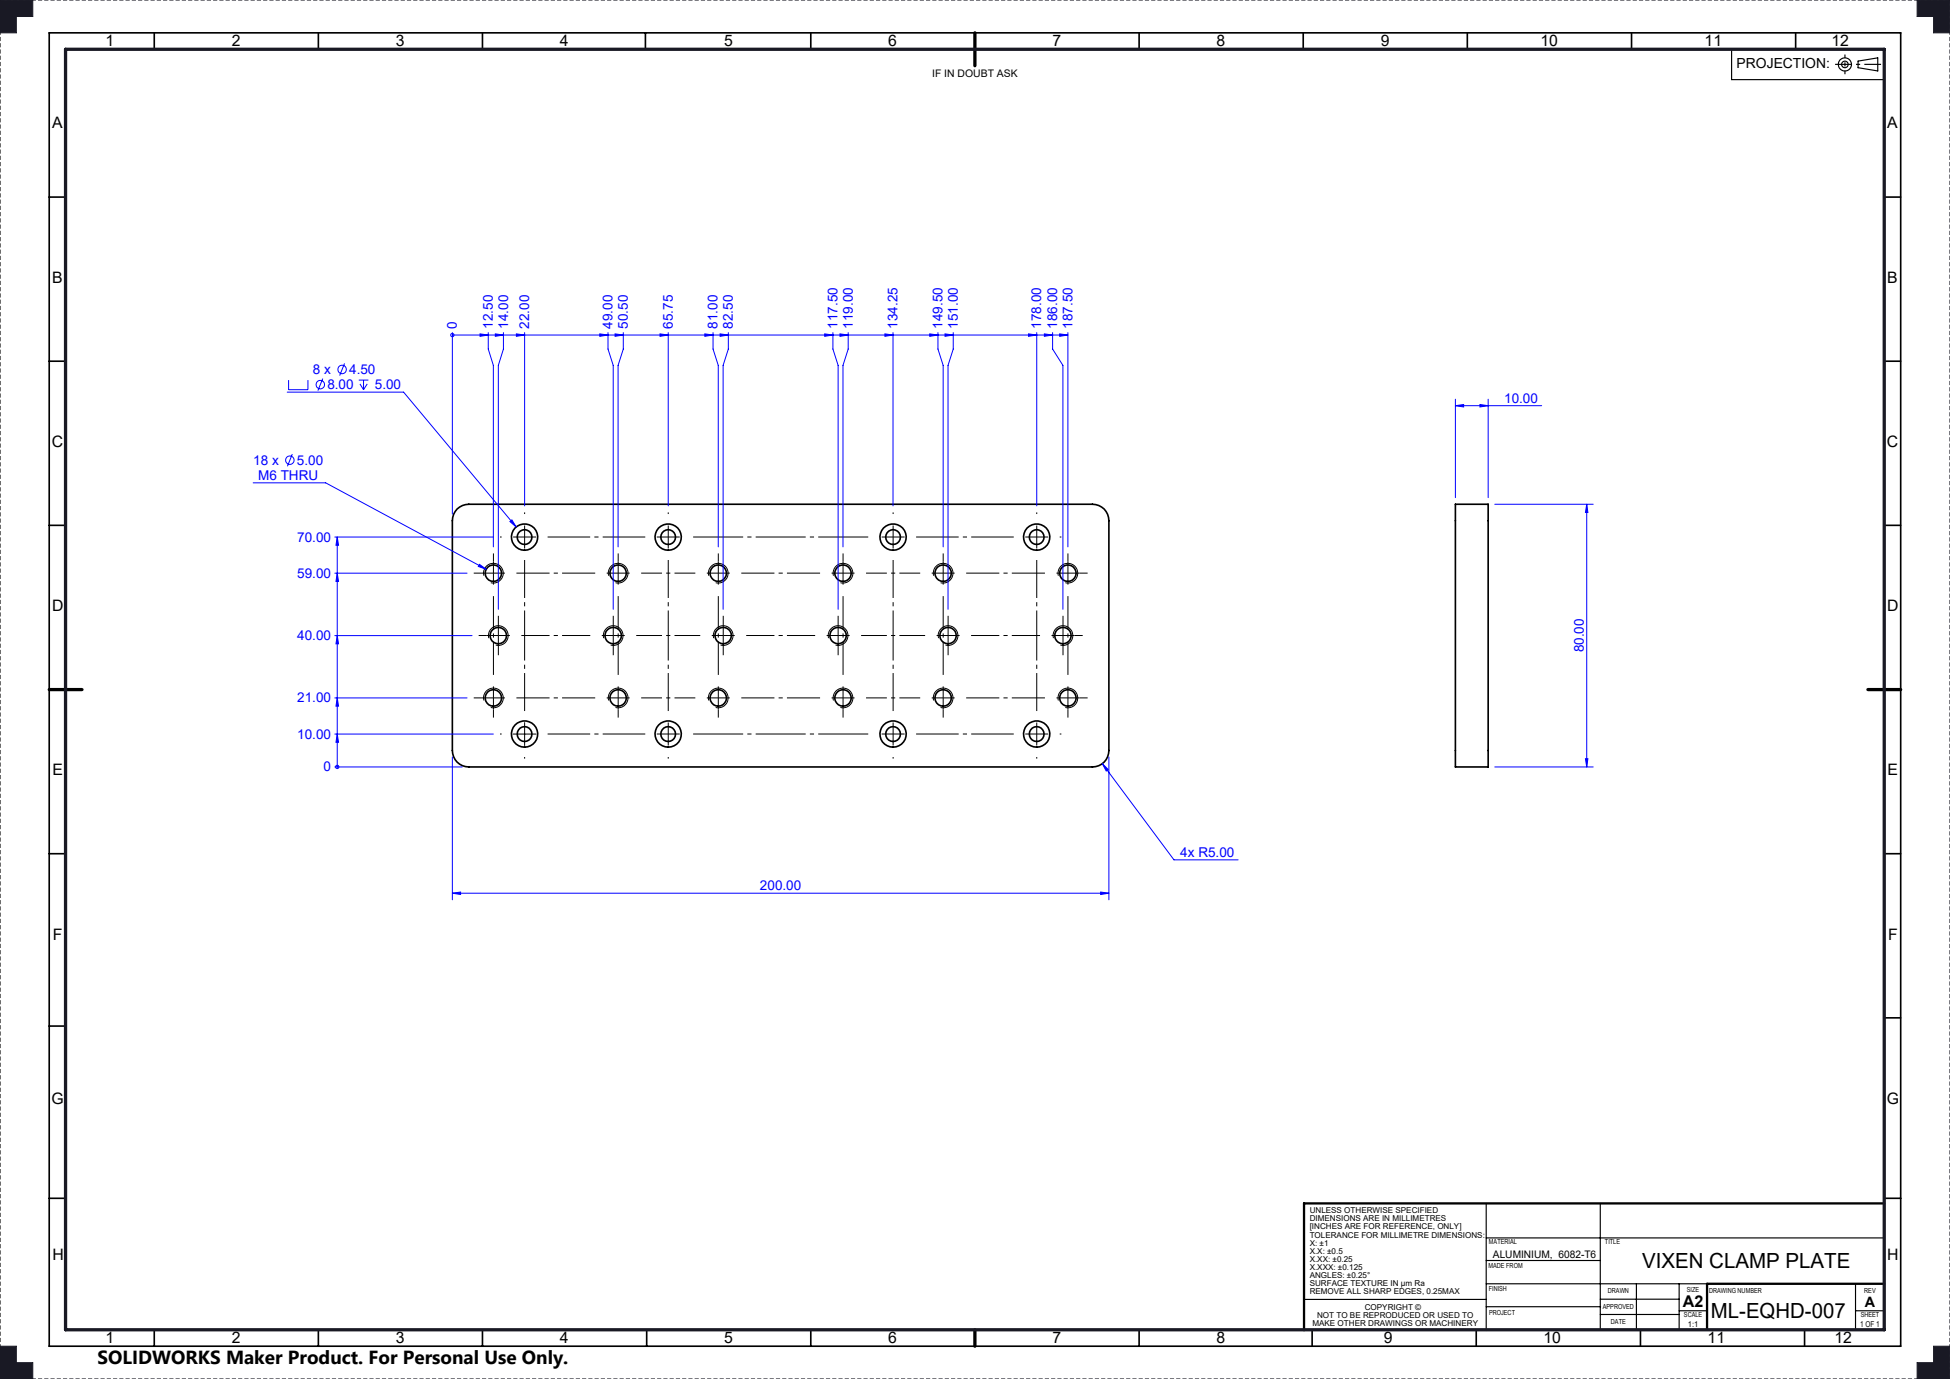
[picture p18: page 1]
18 x 5.00 M6 THRU; COPYRIGHT ©; ALUMINIUM, 6082-T6 MADE FROM; DRAWING NUMBER; SCALE; ML-EQHD-007 A

IF IN DOUBT ASK

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

VIXEN CLAMP PLATE

NOT TO BE REPRODUCED OR USED TO
MAKE OTHER DRAWINGS OR MACHINERY

SOLIDWORKS Maker Product. For Personal Use Only.

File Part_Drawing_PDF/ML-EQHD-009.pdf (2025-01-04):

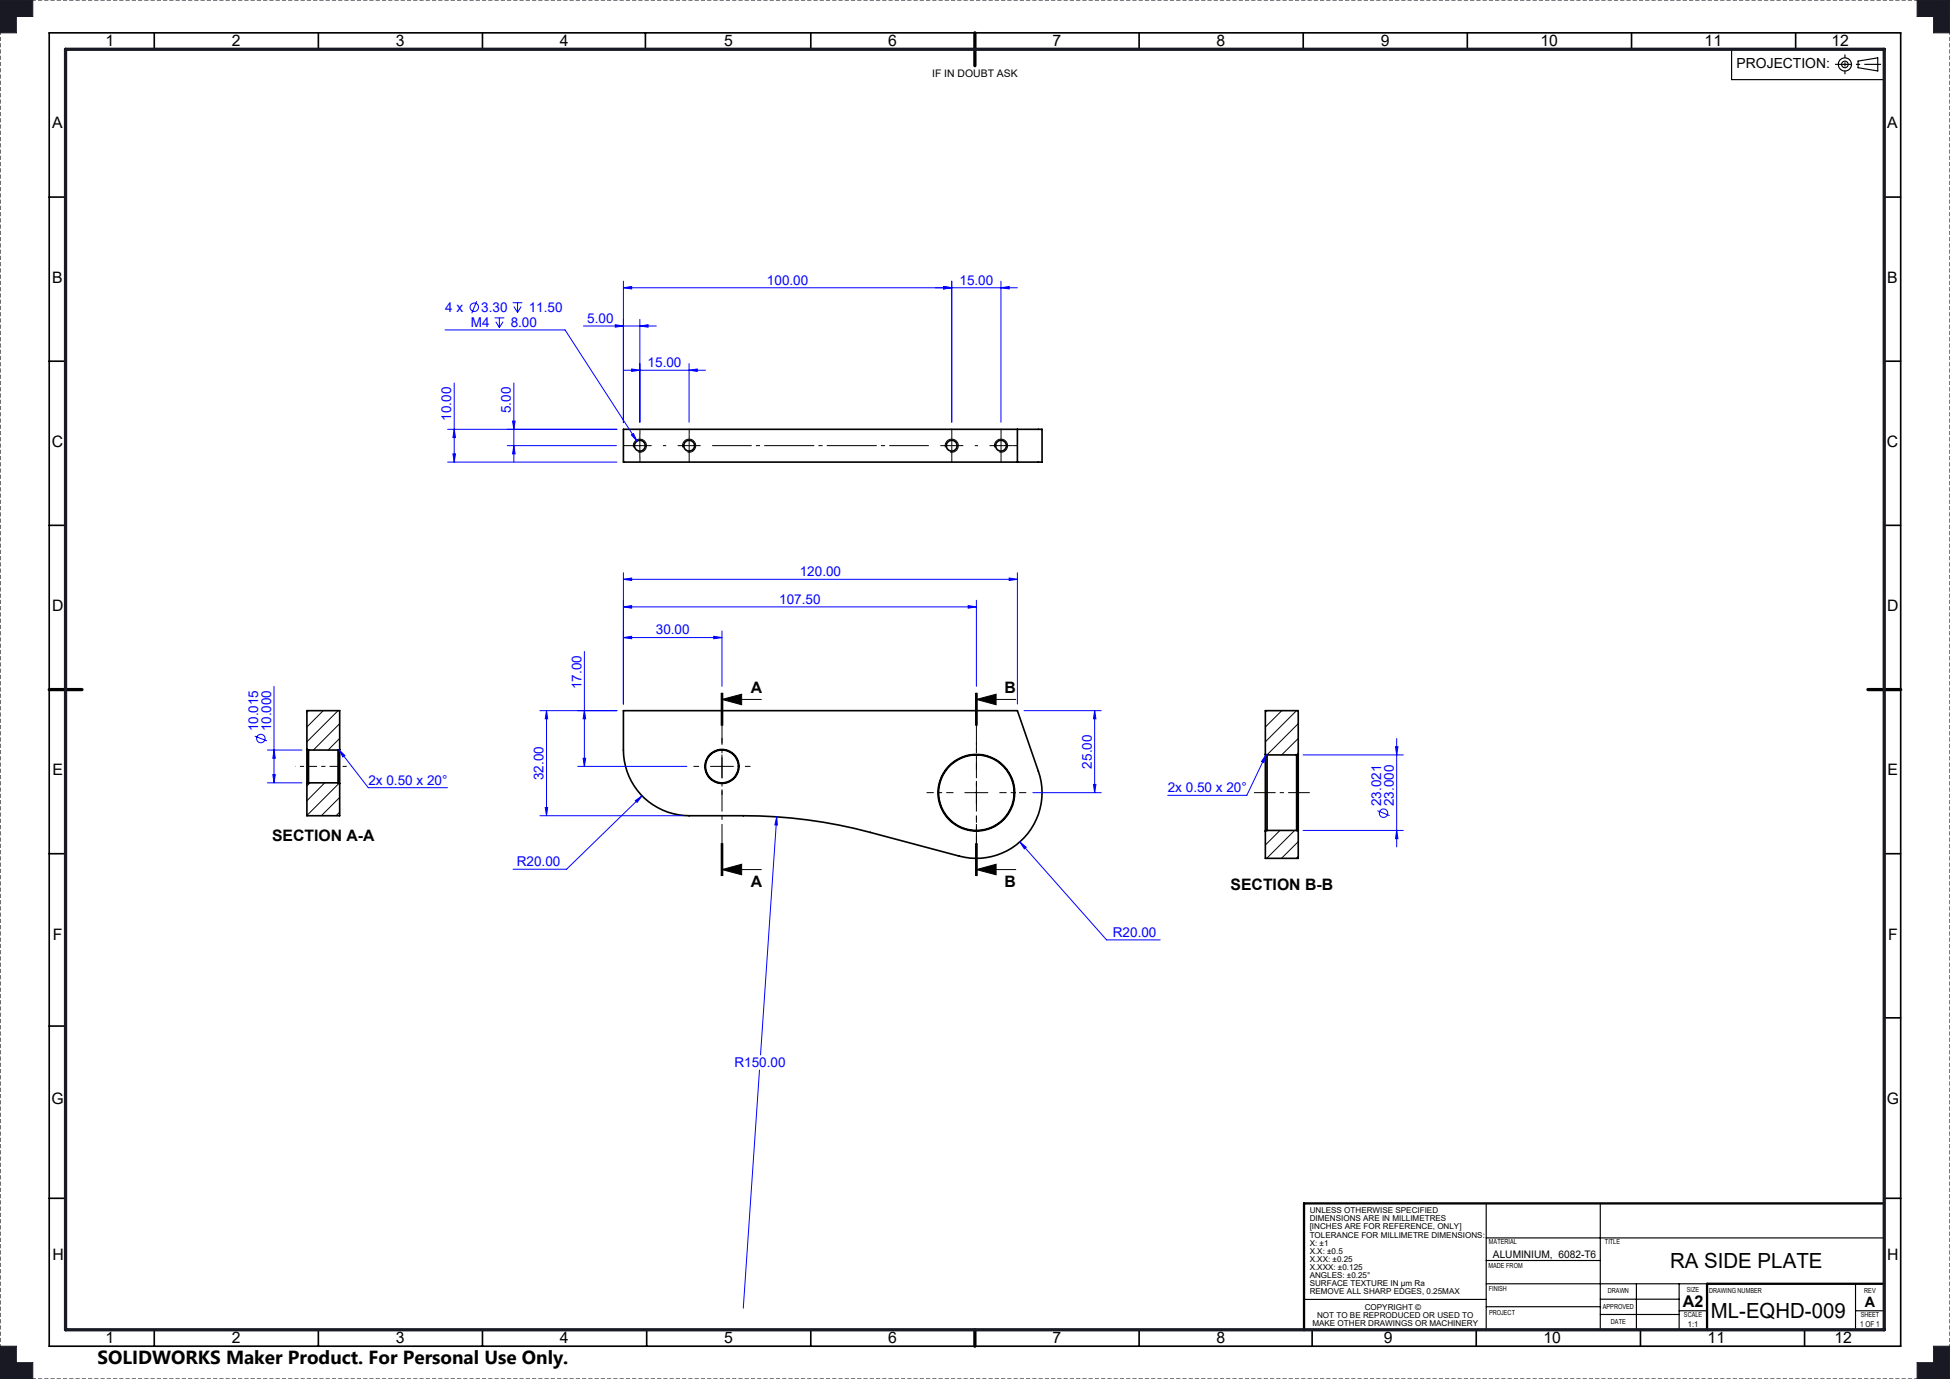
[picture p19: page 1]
SECTION A-A; SECTION B-B; COPYRIGHT ©; ALUMINIUM, 6082-T6 MADE FROM; DRAWING NUMBER; SCALE; ML-EQHD-009 A

IF IN DOUBT ASK

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

RA SIDE PLATE

NOT TO BE REPRODUCED OR USED TO
MAKE OTHER DRAWINGS OR MACHINERY

SOLIDWORKS Maker Product. For Personal Use Only.

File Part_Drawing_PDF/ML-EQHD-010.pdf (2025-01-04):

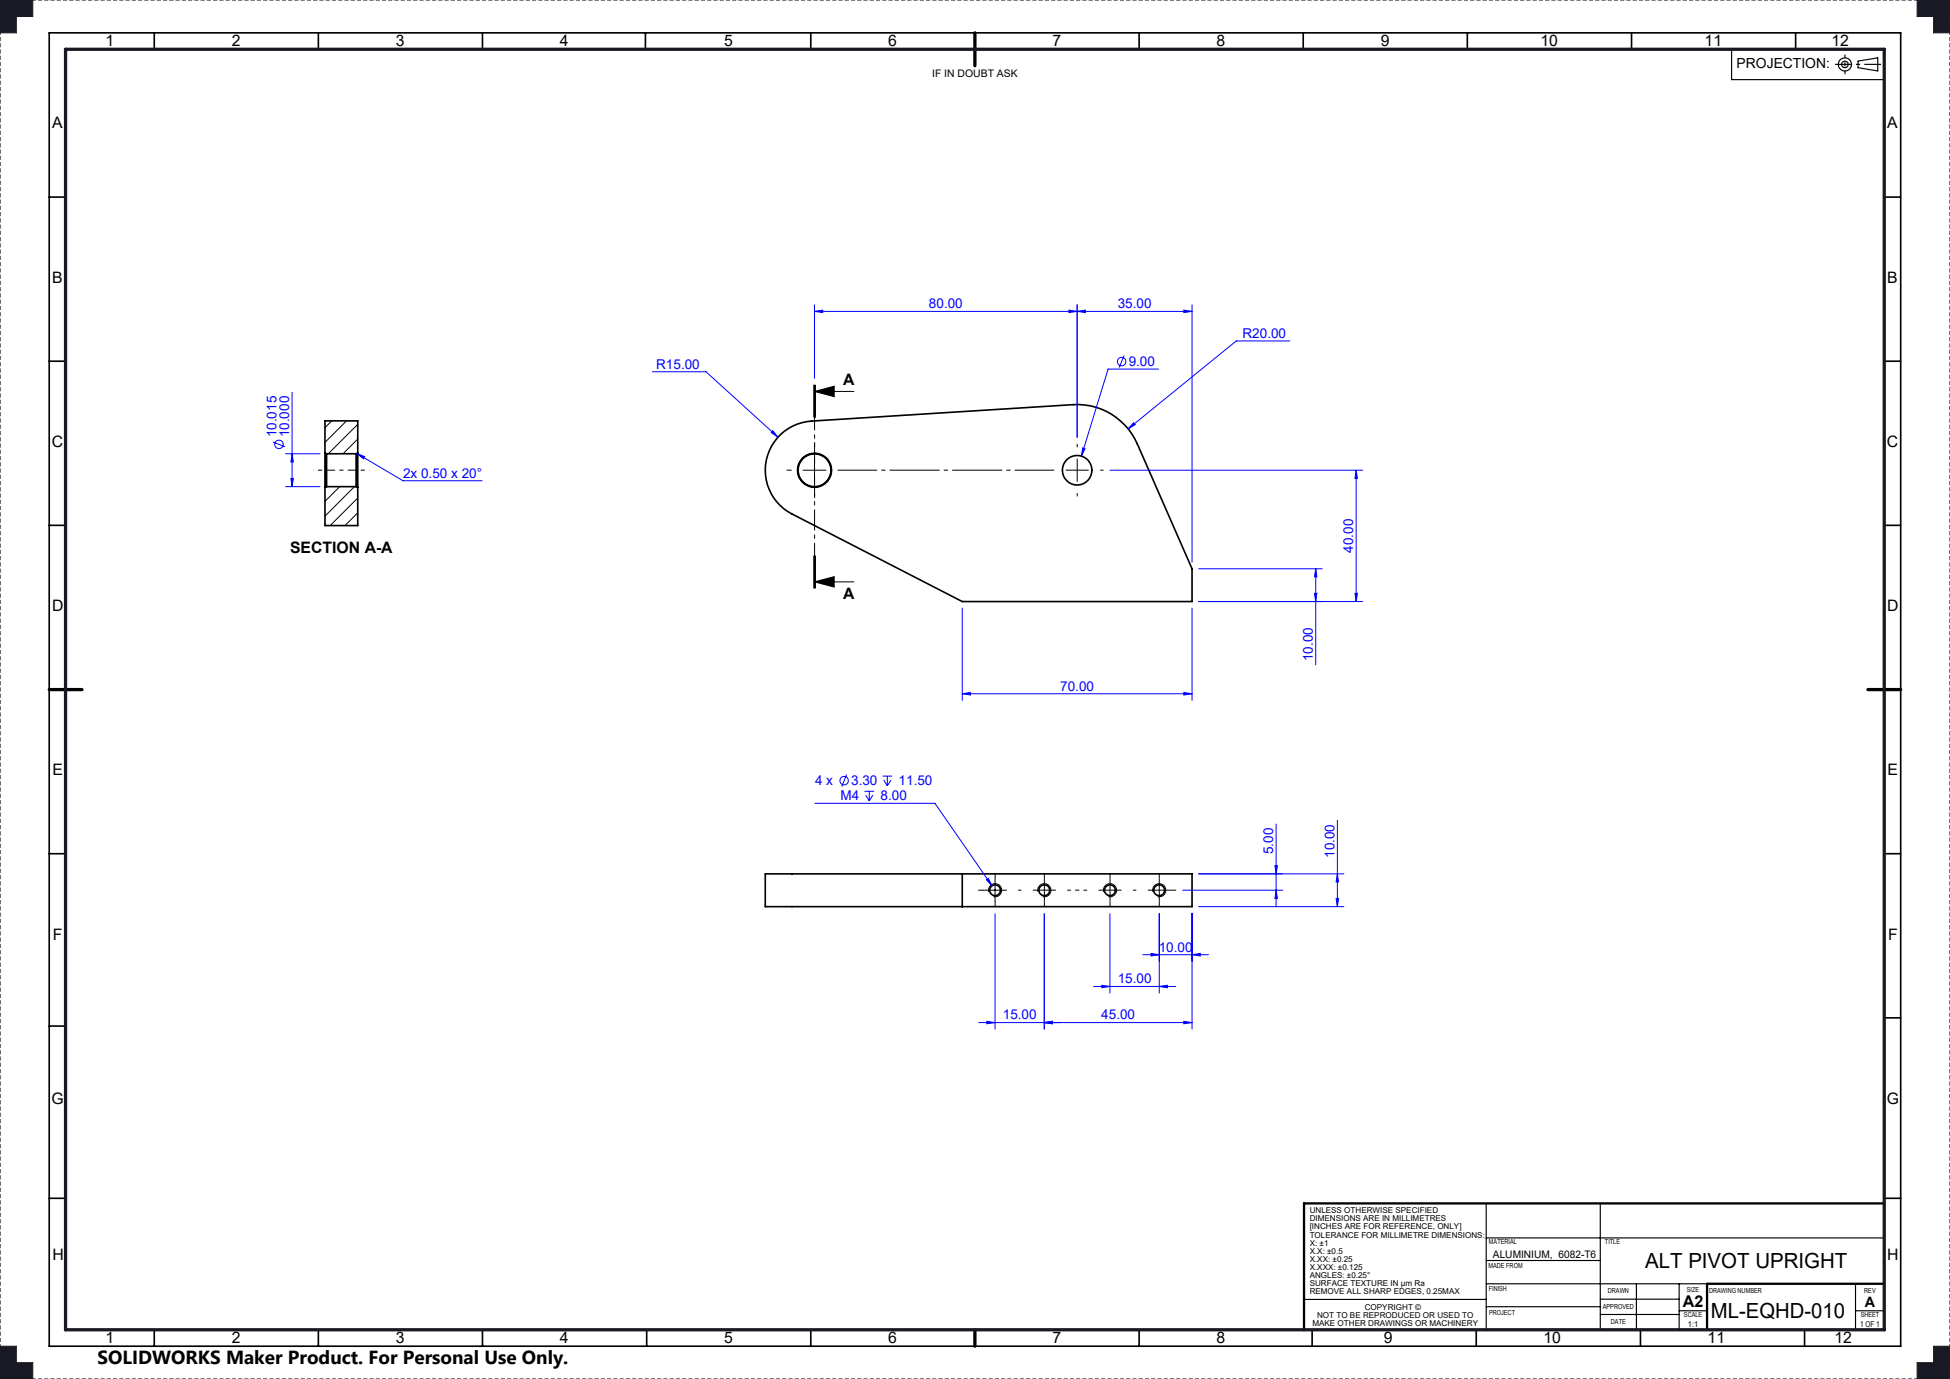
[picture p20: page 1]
SECTION A-A; COPYRIGHT ©; ALUMINIUM, 6082-T6 MADE FROM; DRAWING NUMBER; SCALE; ML-EQHD-010 A

IF IN DOUBT ASK

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

ALT PIVOT UPRIGHT

NOT TO BE REPRODUCED OR USED TO
MAKE OTHER DRAWINGS OR MACHINERY

SOLIDWORKS Maker Product. For Personal Use Only.

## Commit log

2025-01-04 Rename Mount Complete.STEP to Complete_Assembly/Mount Complete.STEP
    [Mount Complete.STEP]
2025-01-04 Rename Mount Complete.x_t to Complete_Assembly/Mount Complete.x_t
    [Mount Complete.x_t]
2025-01-04 Update and rename Mount Complete.STEP to Mount Complete.STEP
    [Mount Complete.STEP]
2025-01-04 Update and rename Mount Complete.x_t to Mount Complete.x_t
    [Mount Complete.x_t]
2025-01-04 Rename Axis Box MC Parts.SLDASM to Solidworks_Makers_Files/Axis Box MC Parts.SLDASM
    [Axis Box MC Parts.SLDASM]
2025-01-04 Rename Mount Complete.STEP to Complete_Assembly_Neutral/Mount Complete.STEP
    [Mount Complete.STEP]
2025-01-04 Update and rename ML-EQHD-020 3D Print Al.STEP to 3D_Print_Aluminium/ML-EQHD-020 3D Print Al.STEP
    [ML-EQHD-020 3D Print Al.STEP]
